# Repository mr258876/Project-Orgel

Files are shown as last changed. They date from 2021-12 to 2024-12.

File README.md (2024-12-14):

# Project Orgel
>### 赛博音乐盒计划第一部分
>### Cyber Musicbox Project Part I

- [中文](#中文)
- [English](#english)

# 中文
>## 目录
- [项目状态](#项目状态)
- [配件](#配件)
- [某个简短的改装指南](#某个简短的改装指南)
    - [传动改造](#传动改造)
    - [八音盒及电机的固定](#八音盒及电机的固定)
    - [电路搭建](#电路搭建)
- [控制程序烧录](#控制程序烧录)
- [使用指南](#使用指南)
    - [初次使用](#初次使用)
    - [基本操作](#基本操作)
    - [菜单与设置](#菜单与设置)
    - [无线控制](#无线控制)

>## 项目状态
* 基础原理验证 ✔
* 基础 UI ✔
* 更多可在UI中调节的值 ✔
* UI 多语言支持 ✔
* 项目自述 ✔
* 无线控制 ✔
* 多平台支持 ✔

>## 配件
* 八音盒 (废话) *1
* 支持串口通信的单片机 *1
>ℹ注：推荐使用ESP32或nRF51802
* TMC2209 步进电机驱动模块 *1
>⚠注意：模块需要支持以串口方式与MCU进行通信
* 42BYGH40/39 步进电机 (高40/39mm) *1  
>ℹ注：可以是任意两相四线步进电机, 但其应能够提供足够力矩(推荐300mN\*m以上)
* 42步进电机支架 (可选) *1
* 0.4模齿轮(60齿以上，但不宜过大) *1
>ℹ注：齿轮越大越好，降低电机转速是减小噪音的有效方法
<br/>⚠注意：齿轮需要能够与电机输出轴匹配
* 旋转编码器 *1
* SSD1306 0.96 寸 OLED 模块 *1
* 电源 (Plan A): USB-C PD 诱骗器 *1, 支持PD快充协议的充电器 *1, MP1584 DC-DC 降压模块 *1
* 电源 (Plan B): 3.3/5/12v 多路输出电源模块 *1, 12v/2A 电源适配器 *1
* 用于固定八音盒与电机的木盒、木块等 *1
* 用于固定的M3螺丝、M3螺母若干

## 某个简短的改装指南
接下来的步骤组成了一个简短的安装指南。步骤供参考，可根据实际情况进行调整。
### 传动改造
如图所示，改装电动只需使用八音盒传动部分中的部分齿轮。由于避开了传动部分中的易损齿轮，对该齿轮损坏的八音盒进行改装不失为一个绝佳选择。
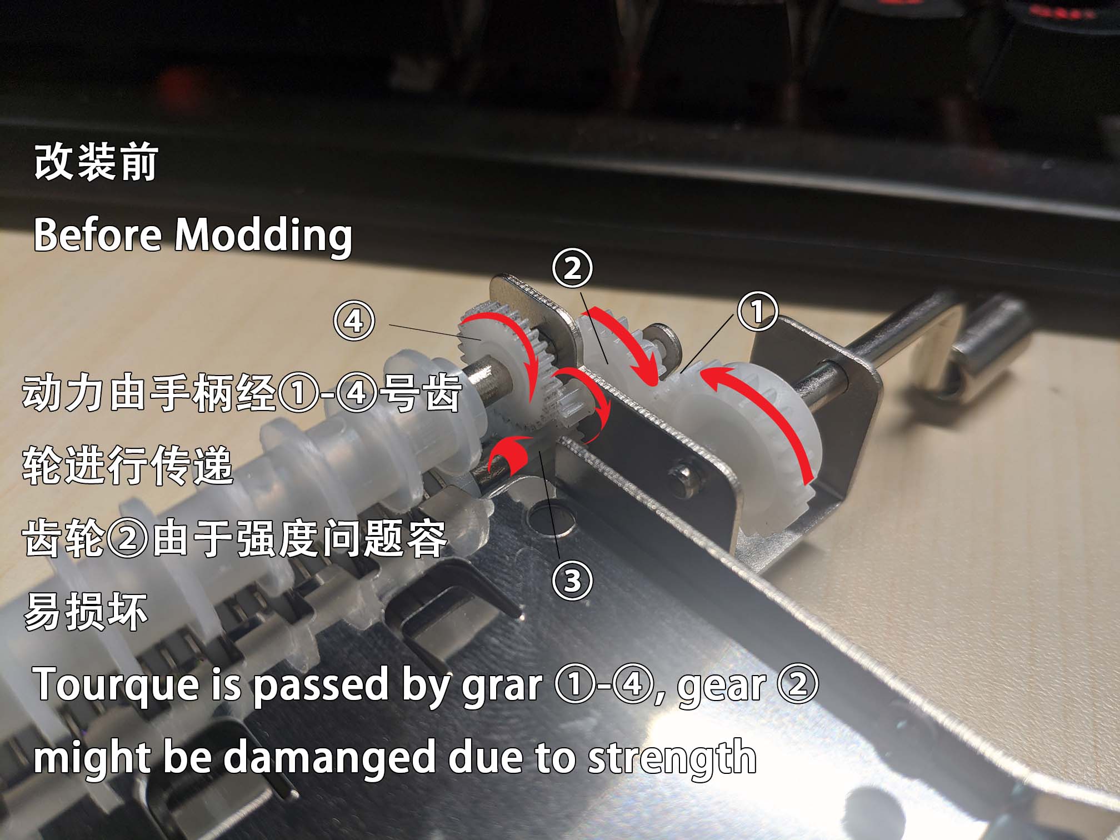
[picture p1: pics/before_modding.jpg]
before_modding

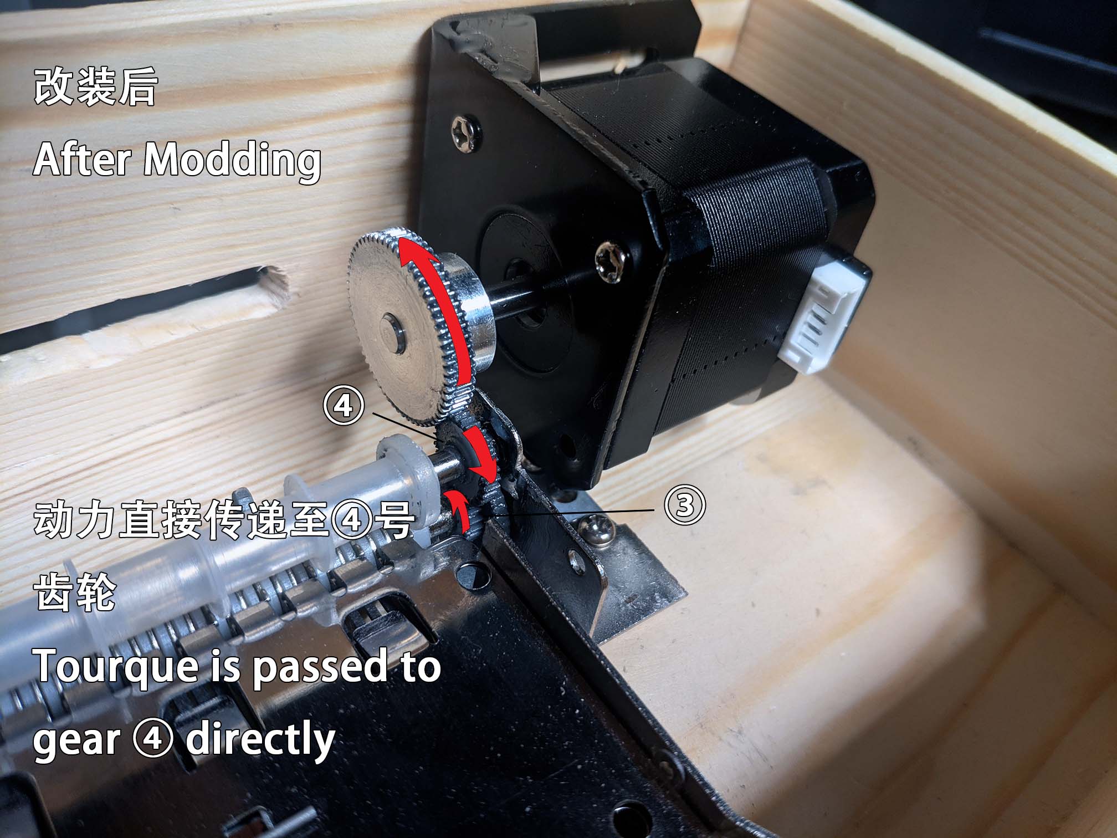
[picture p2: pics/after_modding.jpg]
after_modding


>⚠注意：在手摇八音盒中，手柄部分通常为噪音的源头之一。为了达到静音目的，断开手柄与其他齿轮间的传动是必要的。移除手柄或②号齿轮均可实现。图为移除了手柄及②号齿轮的八音盒。
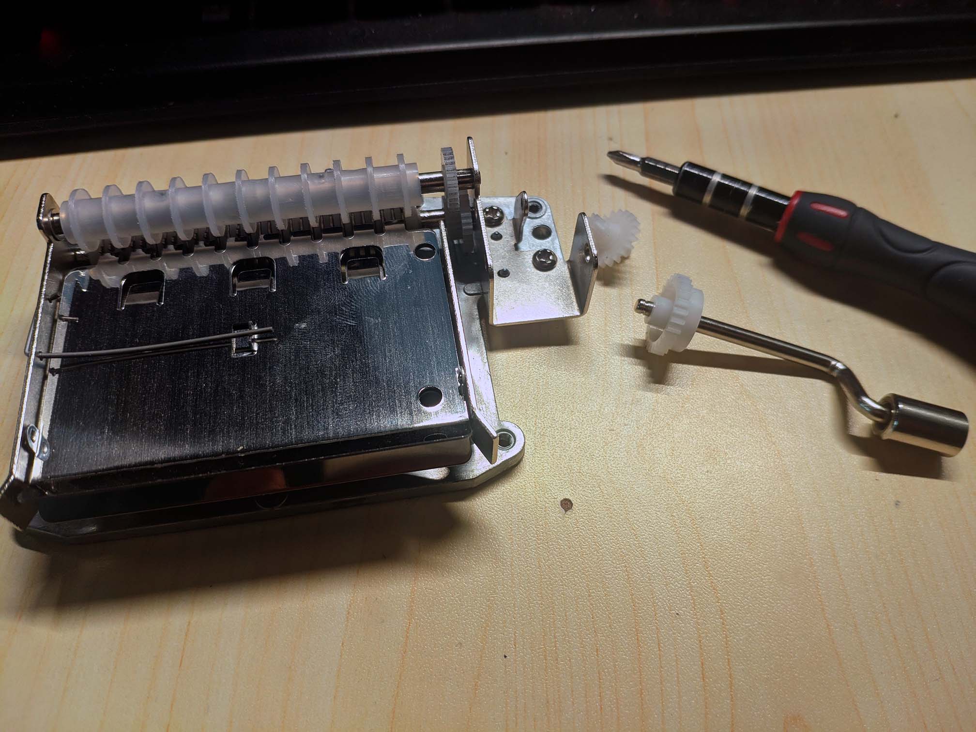
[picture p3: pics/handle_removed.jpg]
handle_removed

### 八音盒及电机的固定
毫无疑问，电机需要与八音盒固定在一起以进行传动。该部分有较多方案可供选择，故此处将不做较多阐述，实际应用时可不必遵照。

>⚠注意：不论以何种方式固定，**电机齿轮必须尽量与八音盒齿轮紧密配合**，否则可能会产生噪音并损坏齿轮。

考虑到八音盒可能需要一个共鸣腔，推荐将八音盒与电机固定在木盒中。如不考虑共鸣，或不方便对木盒进行钻孔/开槽，则也可固定在木块或其他材料上。此处以固定在木盒中为例。

由于42电机的体积较大，因此八音盒原配木盒大概率需要进行更换。目前市面上有多种尺寸木盒可供选择。上一节示例中的木盒尺寸为 长20cm\*宽13.5cm*高9cm。

#### 使用3D打印支架进行固定

项目提供了提供一个支架3D模型可进行参考。支架由两部分组成，分别负责替换原有支架与步进电机的固定。

[模型可在此下载](/Models/)

### 电路搭建

本项目提供两个不同平台版本：一个较为简易的使用ESP32开发板与其他现成部件进行搭建的版本，与一个从零开始构建的nRF51平台版本。您可以根据实际需要进行选择。

#### ESP32版本
`ESP32`版本基于现成部件，电路十分简单，如下图所示。

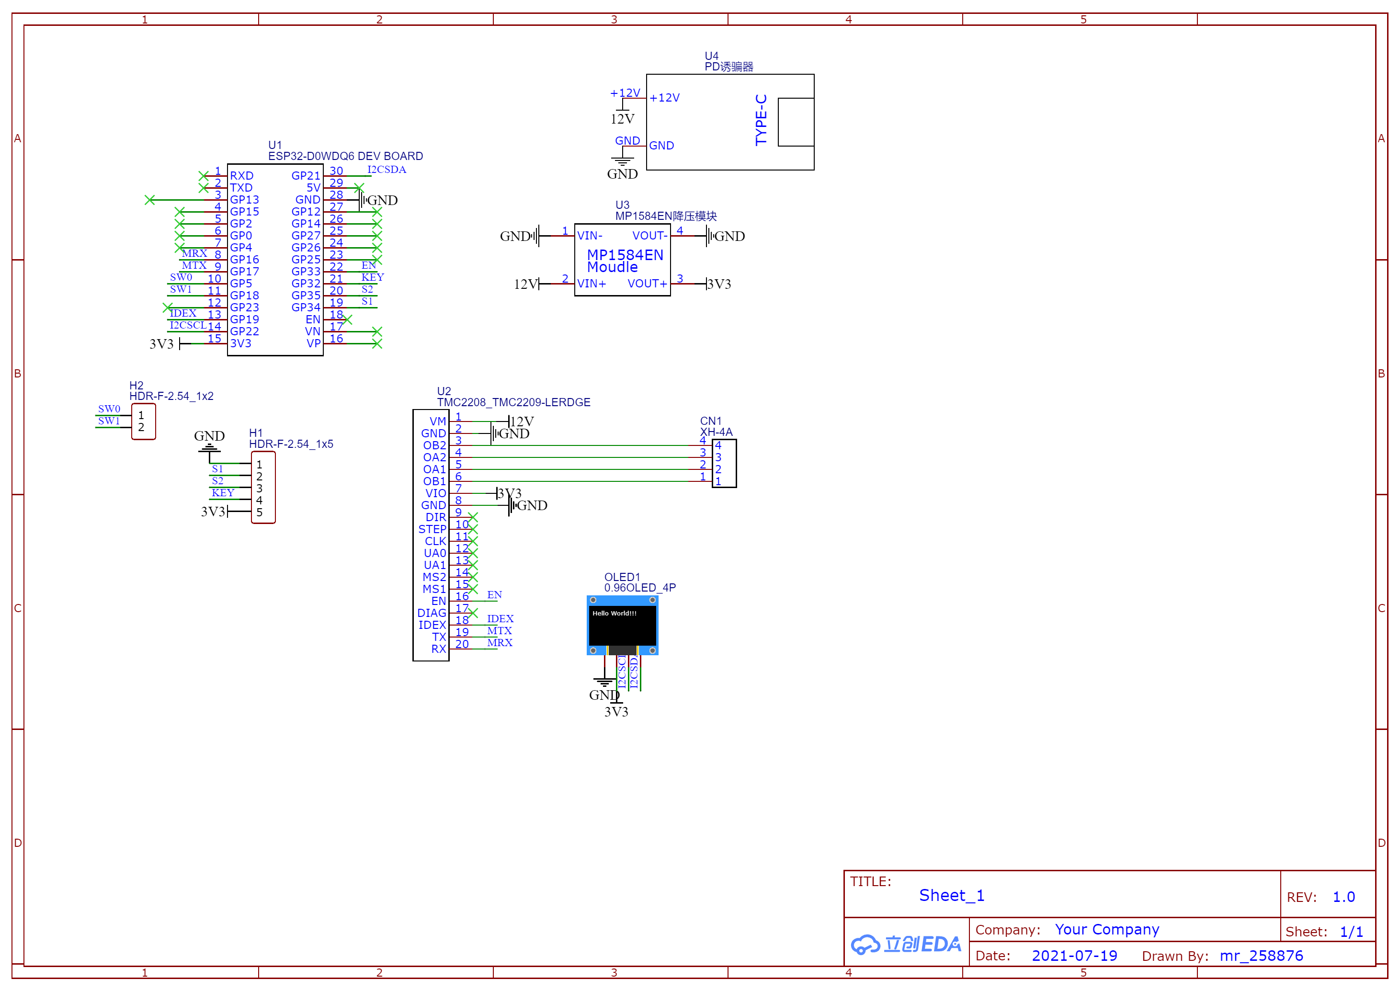
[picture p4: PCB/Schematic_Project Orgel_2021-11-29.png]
curcit_schema


处于空间利用方面的考量，推荐使用PCB实现上图中电路。[Gerber文件请点击这里][gerber_url]。
>ℹ注：仅适用于尺寸为22mm\*17mm的MP1584模块与焊接了TX,RX针脚的乐积TMC2209模块

如果无法进行焊接，该版本同样可以考虑使用面包板完成接线。

**ESP32版本参考BOM**
- 以下链接仅供参考，您可以根据实际情况自行购买
- 链接可能失效，如需更新请提起issue

| 商家 | 商品链接 | 款式 | 价格 (CNY) | 数量 | 备注 |
| ---- | ---- | ---- | ---- | ---- | ---- |
| 尚雅木艺 | [实木带锁复古收纳盒定制长方形大小号木盒子定做木质包装盒礼品盒](https://item.taobao.com/item.htm?id=610812897067) | 20\*13.5\*9 | 17.9 | 1 | 需自行开孔/开槽 (大概是整个项目最困难的部分) |
| 淮安善能机械有限公司 | [0.4模 60齿 孔5/6 顶丝 善能机械 铝齿轮 齿轮定制 小模数齿轮](https://item.taobao.com/item.htm?id=587174945136) | 60齿外径24.8/齿厚4/孔5台阶顶丝 | 9 | 1 | 不包邮 |
| 信泰微电子 | [ESP32-D0WDQ6开发板 蓝牙+WIFI模块 Lua物联网 米思齐图形化编程](https://item.taobao.com/item.htm?id=647797965965) | 30针 | 19.8 | 1 | 可能不太好找同款 |
| 信泰微电子 | [数字旋转编码器模块 转动电位器 旋转电位器 带旋钮帽](https://item.taobao.com/item.htm?id=576520367466) | - | 3.8 | 1 | - |
| 信泰微电子 | [0.96寸蓝色 黄蓝双色 白色 I2C IIC通信 显示器 OLED液晶屏模块](https://item.taobao.com/item.htm?id=43639171586) | 新款 颜色任意 | 10 | 1 | - |
| 信泰微电子 | [DC-DC 电源模块 降压稳压模块 车载电源 12V 5V转3.3V 固定输出](https://item.taobao.com/item.htm?id=534263863865) | - | 2.5 | 1 | - |
| 信泰微电子 | [XH2.54 2.54mm间距 白色座 接插件 直针座 4P XH2.54-4P连接线座](https://item.taobao.com/item.htm?id=36638833821) | - | 0.05 | 1 | 实际需要1个,但是不知道只买1个发不发货 |
| 微盛恒创电子 | [PD2.03.0诱骗器 触发转接笔记本电压可调9V12V15V 20VTYPE-C母头](https://item.taobao.com/item.htm?id=643246818193) | 12V | 4.8 | 1 | - |
| 乐积科技 | [3D打印机配件 TMC2209驱动大电流高细分替换2208A4988 LV8729模块](https://item.taobao.com/item.htm?id=610229295552) | - | 18.6 | 1 | 需要补齐四根空脚 |
| 布加特官方店 | [42/57步进电机支架安装固定座卧式支架电机马达支架座配带螺丝](https://item.taobao.com/item.htm?id=571691530940) | - | 1.7 | 1 | - |
| 布加特官方店 | [3D打印机配件42步进电机 驱动马达两相四线1.8度雕刻机42歩进马达](https://item.taobao.com/item.htm?id=559102944871) | 任意款式 XH-2.54配线 | 21.5 | 1 | - |
| telesky旗舰店 | [单排母双排母2.54mm排针母座排座针插座插针2.0 1/2/3/4/6/10-40P](https://item.taobao.com/item.htm?id=559102944871) | 1*2p单排母座2.54mm 20个 | 2.44 | 1 | 可选, 实际需要2个 |
| telesky旗舰店 | [单排母双排母2.54mm排针母座排座针插座插针2.0 1/2/3/4/6/10-40P](https://item.taobao.com/item.htm?id=559102944871) | 1*4p单排母座2.54mm 20个 | 2.75 | 1 | 可选, 实际需要1个 |
| telesky旗舰店 | [单排母双排母2.54mm排针母座排座针插座插针2.0 1/2/3/4/6/10-40P](https://item.taobao.com/item.htm?id=559102944871) | 1*5p单排母座2.54mm 20个 | 2.98 | 1 | 可选, 实际需要1个 |
| telesky旗舰店 | [单排母双排母2.54mm排针母座排座针插座插针2.0 1/2/3/4/6/10-40P](https://item.taobao.com/item.htm?id=559102944871) | 1*8p单排母座2.54mm 20个 | 3.59 | 1 | 可选, 实际需要2个 |
| telesky旗舰店 | [单排母双排母2.54mm排针母座排座针插座插针2.0 1/2/3/4/6/10-40P](https://item.taobao.com/item.htm?id=559102944871) | 1*15p单排母座2.54mm 10个 | 2.52 | 1 | 可选, 实际需要2个 |

#### nRF51版本
`nRF51`版本将主控、步进电机驱动、DCDC电路等部分集成在一块PCB上，进而减小了控制板体积，但同时也提升了制作难度。电路图如下所示。

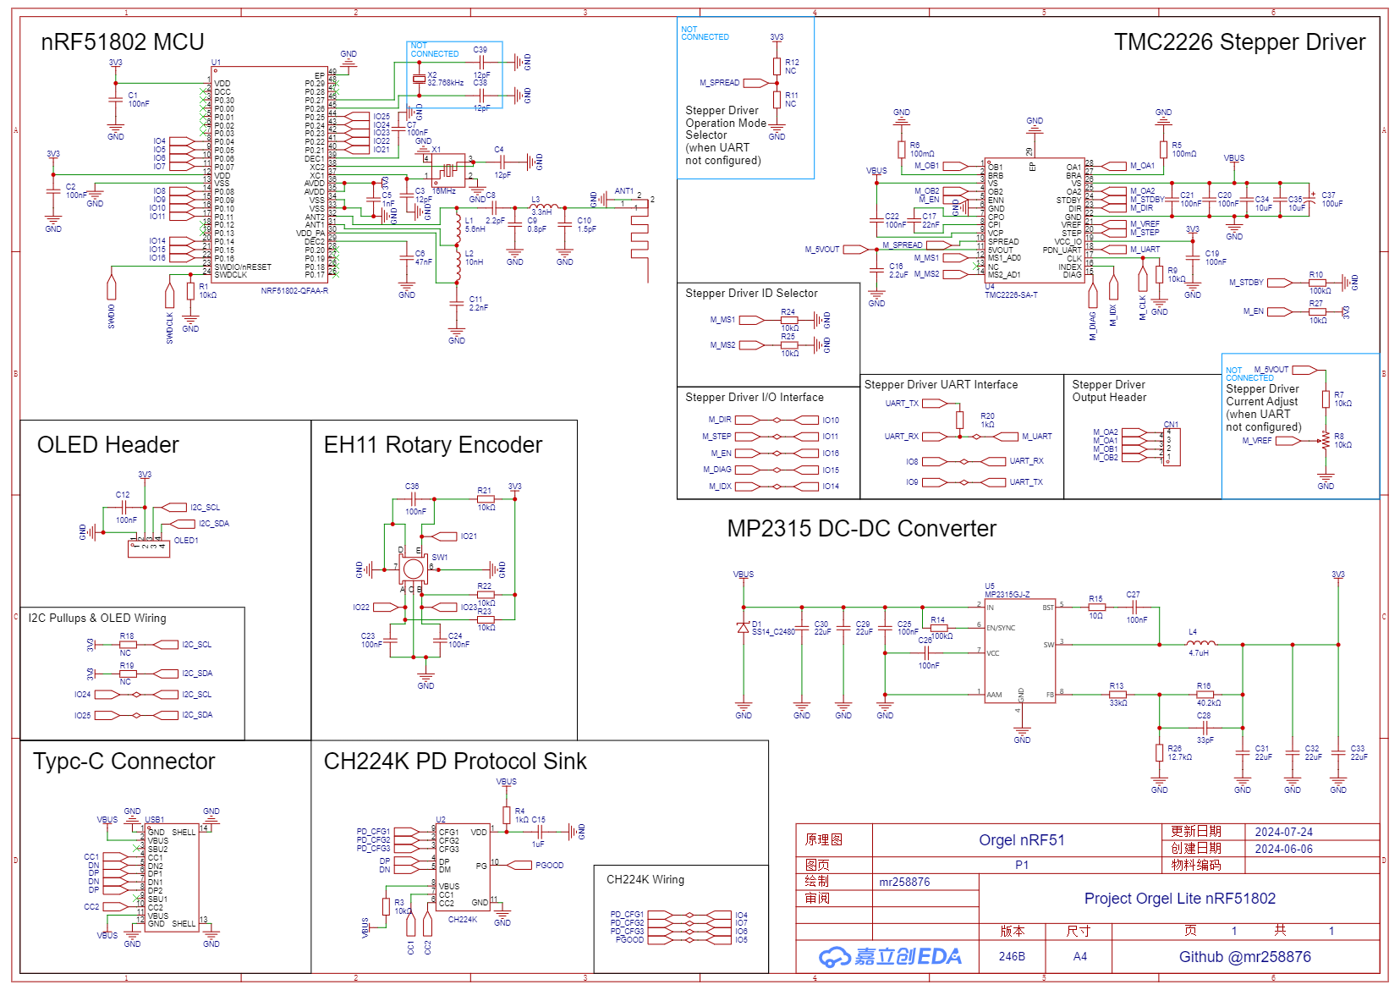
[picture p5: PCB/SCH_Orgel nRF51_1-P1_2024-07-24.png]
curcit_schema_nrf51


**项目BOM**

[项目BOM可在此处查看。][bom_url_nrf51]

**参考PCB**

[参考PCB可以在此处下载。][gerber_url_nrf51]

**焊接辅助工具**

[此处可查看对应焊接辅助工具。][solder_helper_url_nrf51]

## 控制程序烧录
改装的最后一步是将电机控制程序烧录至`ESP32`或`nRF51802/nRF51822`中。

您可以直接刷入 Release 中已编译好的固件，或自行使用Arduino编译并刷入。

### 刷入预编译固件

#### 为ESP32刷入预编译固件

0. 移步[乐鑫科技网站]("https://www.espressif.com.cn/zh-hans/support/download/other-tools")并下载`ESP Download Tool(Flash下载工具)`。</br>

1. 打开ESP Download Tool，芯片类型选择`ESP32`，工作模式选择`开发模式`。</br>
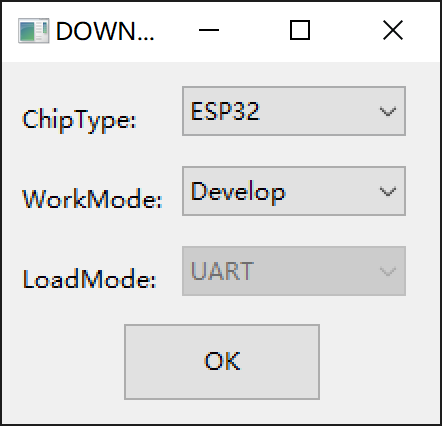
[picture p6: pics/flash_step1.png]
</br>
2. 按照下图设置刷入的文件、flash地址、flash速度，串口及下载速度按实际情况选择。</br>
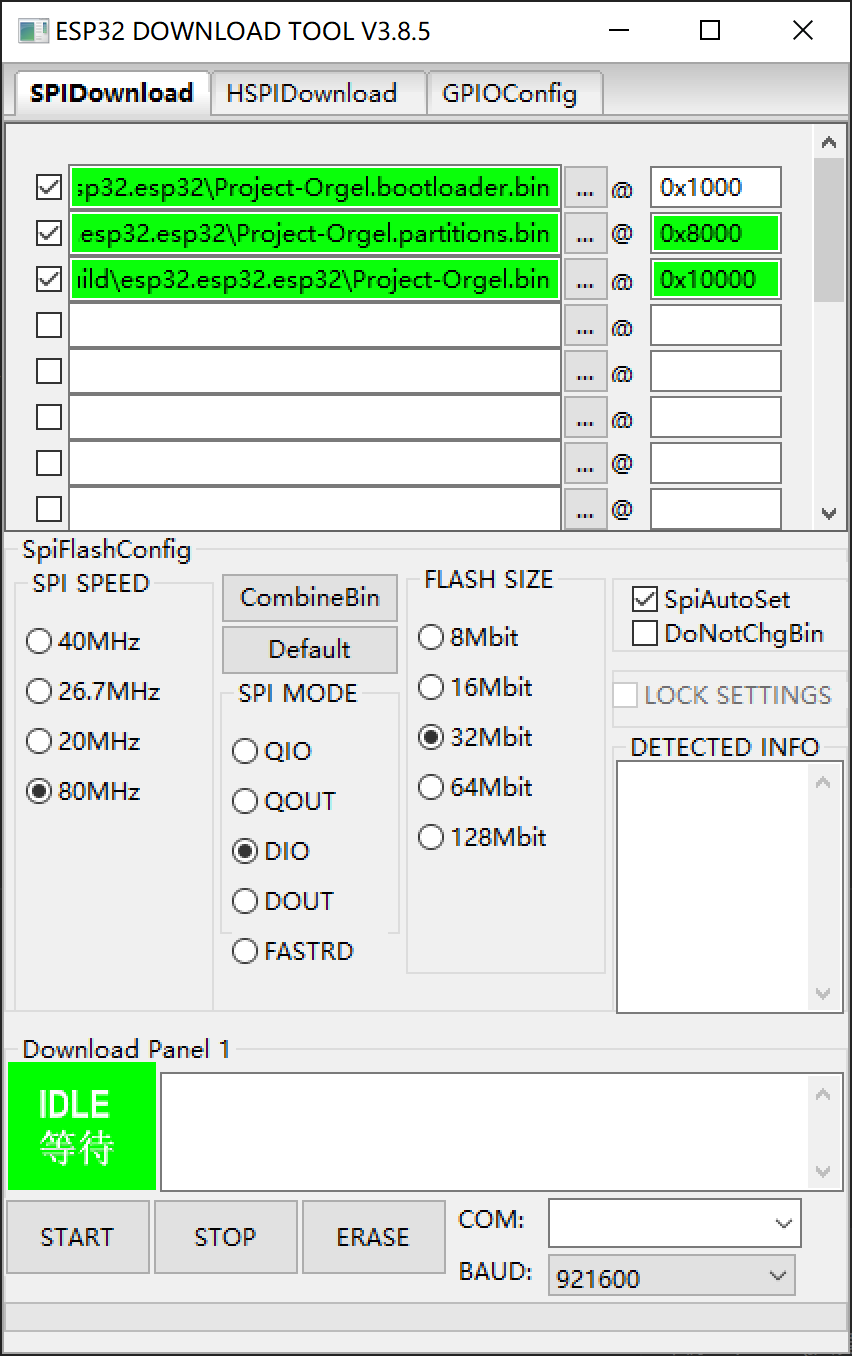
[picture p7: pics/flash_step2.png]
</br>
3. 点击`下载`按钮。当状态显示`完成`后，断开开发板与电脑的连接。</br>

#### 为nRF51刷入预编译固件

>ℹ注：为了向nRF51芯片刷入程序，您额外需要一个适用于ARM架构单片机的编程器，例如`ST-Link`、`J-Link`等。下方的流程以在Windows环境下使用`ST-Link`刷入为例，您可能需要根据实际情况适当修改命令行参数。

0. 移步[OpenOCD Github页面](https://github.com/openocd-org/openocd/releases)，下载并解压`OpenOCD`。</br>
1. 将编程器连接至控制板。
```
编程器             控制板
______         _____________
3V3   | ----> | 3V3   SWCLK | <-----,
GND   | ----> | GND   SWDIO | <--,  |
SWDIO | ----, |_____________|    |  |
SWCLK | --, `--------------------`  |
______|   `-------------------------`
```
2. 打开命令提示符(`CMD`)或`PowerShell`，并切换路径至`OpenOCD`文件夹中的`bin`目录下。</br>
3. 使用以下命令刷入预编译固件。在刷入完成后，命令行中应出现`** Verified OK **`提示。
   - 此处假设`Project-Orgel-nRF51.hex`与`openocd.exe`置于同一目录下。
   - 您可以根据实际情况将`st-link.cfg`替换为其他受支持的编程器配置文件。
```powershell
./openocd.exe -f "interface/st-link.cfg" -f "target/nrf51.cfg" -c "init" -c "reset halt" -c "nrf51 mass_erase" -c "program Project-Orgel-nRF51.hex verify reset exit"
```

### 自行编译并刷入

#### 为ESP32编译程序并刷入
首先需要在电脑上搭建Arduino-ESP32环境。[知乎用户铁熊的文章][zhihu_esp32_environment_url]可供参考。

在环境搭建完成后，还需要在库管理器中安装以下库：
```
tcMenu      @4.4.0
TMCStepper  @0.7.3
U8g2        @2.34.4
NimBLE      @1.4.2
```

准备完成后，使用Arduino IDE打开`Project-Oegel`文件夹中的`Project-Orgel.ino`进行烧录。

>⚠注意：Arduino IDE中的`esp32开发板`版本不可使用`3.0.0`及以上版本！

#### 为nRF51编译程序并刷入

对于`nRF51`版本，您需要将`arduino-esp32`开发环境替换为[n-able-Arduino](https://github.com/h2zero/n-able-Arduino)，具体操作如下：
1. 在`文件`->`首选项`->`附加开发板管理器网址`中添加链接`https://h2zero.github.io/n-able-Arduino/package_n-able_boards_index.json`
2. 待安装完成后，在`工具`->`开发板`->`Arm (Nim)BLE Boards`菜单中选择`Waveshare BLE400`开发板。
3. 在`工具`->`Low Frequency Clock`菜单中选择`Synthesized`选项。
4. 在`工具`->`编程器`菜单中选择`st-link v2`选项。

对于`nRF51`版本，您还需要将上述列表中的`U8g2`库替换为`SSD1306UTF8`库(基于`SSD1306Ascii`库)，请从[此处](https://github.com/mr258876/SSD1306UTF8)下载。

>ℹ注：对于`nRF51`版本，您需要点击`项目`菜单中的`使用编程器上传`选项刷入自编译程序。

## 使用指南
>⚠注意：由于硬件组合及改装操作的多样性，在不同情形下运行可能触发未知的bug，如部分功能不可用等。该指南仅代表在测试硬件上的操作及运行效果。

>🛑警告：步进电机驱动器运行会产生高温。请小心烫伤。

### 初次使用
将程序首次烧录至ESP32时，所有设置为默认初始值0。请遵照下述方法设置`齿轮齿数`、`运行电流`并保存后再使用。
### 基本操作
在主视图中，旋转旋钮更改BPM。单击旋钮切换播放状态。
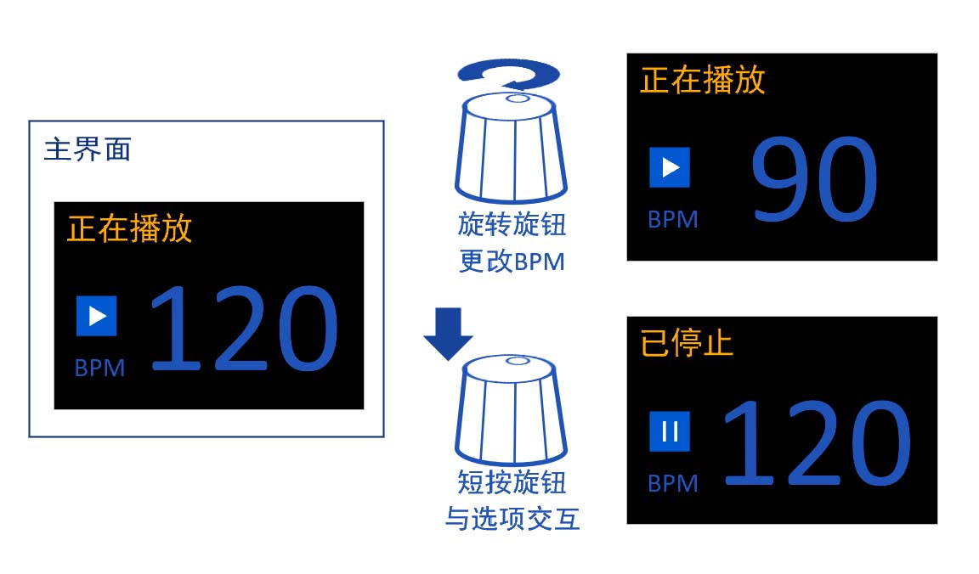
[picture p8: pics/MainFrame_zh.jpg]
mainframe_zh

### 菜单与设置
在主视图中长按可进入主菜单。
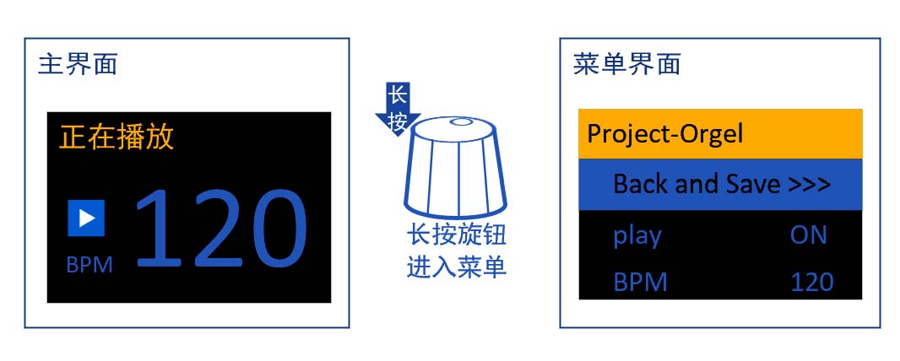
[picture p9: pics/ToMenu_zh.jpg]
tomenu_zh


在主菜单中选择`Back and Save`以保存设置并回到主菜单。在主菜单中无操作30秒会自动返回主界面。

>⚠注意：在更改菜单中选项值后必须通过`Back and Save`选项退出菜单，否则在重启后选项值将恢复更改前状态。

在菜单中旋转旋钮查看选项，单击旋钮以与选项交互。在交互状态下旋转旋钮以更改选项值，单击旋钮退出。
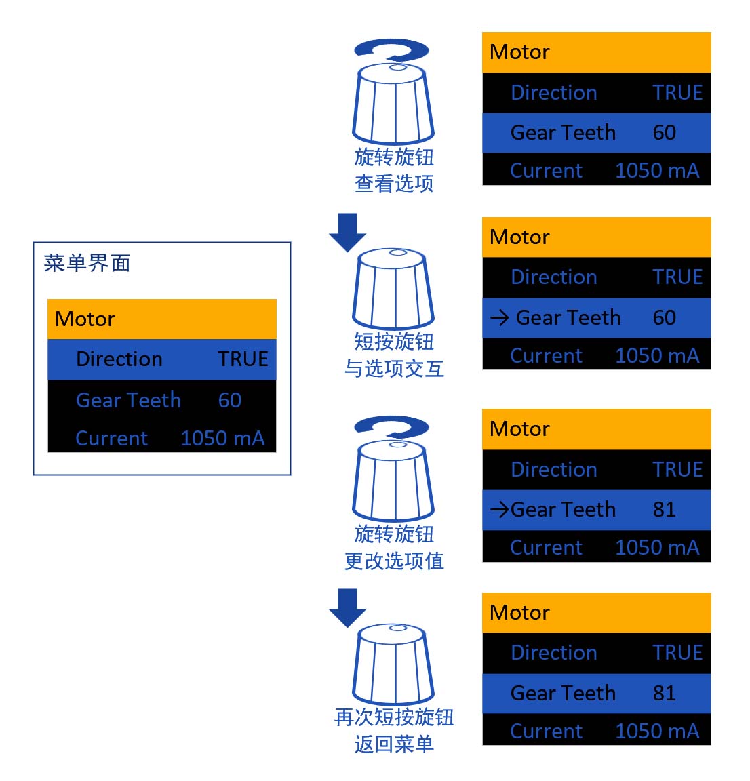
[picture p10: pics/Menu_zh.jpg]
menu_zh


各可调节值说明：
 - 电机设置
     - 反向运转: 控制电机正反转
     - 齿轮齿数: 电机齿轮齿数设置
     - 运行电流: 电机运行电流设置，单位mA 参考值：1050mA
    >⚠注意：随着电流的增大，驱动器会产生更多热量并可能导致过热保护，电机可能会产生更大噪音。正常使用请不要将该值提升至1700mA以上。
 - 语言
     - ENG：英语
     - 中文：简体中文
 - 蓝牙
     - 开：开启蓝牙并启用无线控制功能
     - 关：关闭蓝牙并停用无线控制功能

### 无线控制

> 请打开设置中的蓝牙开关，随后访问[https://mr258876.github.io/Project-Orgel/](https://mr258876.github.io/Project-Orgel/)并按提示操作。

Have fun!

# English
>## Table of Contents
- [Project Orgel](#project-orgel)
- [中文](#中文)
  - [某个简短的改装指南](#某个简短的改装指南)
    - [传动改造](#传动改造)
    - [八音盒及电机的固定](#八音盒及电机的固定)
      - [使用3D打印支架进行固定](#使用3d打印支架进行固定)
    - [电路搭建](#电路搭建)
      - [ESP32版本](#esp32版本)
      - [nRF51版本](#nrf51版本)
  - [控制程序烧录](#控制程序烧录)
    - [刷入预编译固件](#刷入预编译固件)
      - [为ESP32刷入预编译固件](#为esp32刷入预编译固件)
      - [为nRF51刷入预编译固件](#为nrf51刷入预编译固件)
    - [自行编译并刷入](#自行编译并刷入)
      - [为ESP32编译程序并刷入](#为esp32编译程序并刷入)
      - [为nRF51编译程序并刷入](#为nrf51编译程序并刷入)
  - [使用指南](#使用指南)
    - [初次使用](#初次使用)
    - [基本操作](#基本操作)
    - [菜单与设置](#菜单与设置)
    - [无线控制](#无线控制)
- [English](#english)
  - [Hardware Requirements](#hardware-requirements)
  - [A Brief Modding Guide](#a-brief-modding-guide)
    - [Gear Modding](#gear-modding)
    - [Mounting](#mounting)
    - [Circuit](#circuit)
    - [Uploading Code](#uploading-code)
      - [Flash the compiled firmware](#flash-the-compiled-firmware)
      - [Compile and flash by yourself](#compile-and-flash-by-yourself)
  - [Usage](#usage)
    - [First Use](#first-use)
    - [Basic Operations](#basic-operations)
    - [Settings](#settings)
    - [Wireless Control](#wireless-control)

>## Project Status 
* Make it work  ✔
* A Basic UI    ✔
* More Adjustable Values in UI ✔
* UI MultiLanguage Support   ✔
* Readme  ✔
* Wireless Control ✔
* Multi Platform Support ✔

## Hardware Requirements
* Musicbox (of course) *1
* ESP32-D0DWQ6 Dev Moudle 30pin *1
* TMC2209 Stepper Driver Module *1
>⚠Caution: the driver moudlue should be able to communicate with the MCU through UART or Serial port.
* 42BYGH40/39 NEMA17 Stepper *1  
>ℹNote: Could be replaced with any 2-phase 4-wire step motor, however it should provide enough torque(recommand 300mN*m or above).
* NEMA17 Motor Stand (optional) *1
* 0.4M gear(At least 60 teeth, but not too big) *1  
>ℹNote：It is a good idea to have a bigger gear, reducing the motor speed is an effective way to reduce noise.
<br/>⚠Caution: The gear should be able to match the output shaft of the motor.
* Rotatry Encoder *1
* SSD1306 0.96 inch OLED Screen *1
* Power Supply (Plan A): USB-C PD Trigger/Decoy *1, Phone charger with fast charging support *1, MP1584 DC-DC step-down moudle *1
* Power Supply (Plan B): 3.3/5/12v multi-output power moudle *1, 12v/2A AC/DC adapter *1
* Box or something else for mounting musicbox and motor *1
* M3 Screws & Nuts for Mounting

## A Brief Modding Guide
The following steps constitute a biref modding guide, which you could refer to but don’t have to strictly follow.
### Gear Modding
Only some of all gears in the musicbox will be used after the modding, as shown in the picture below. Avoiding the vulnerable gear(gear #2), it is a good choice to mod a musicbox with that gear damaged.
before_modding
after_modding

>⚠Caution：The handle is usually one of the main noise source. In order to get silent, it is necessary to disconnect the transmission between the handle and other gears, which could be implemented by removing the handle or gear #2. A music box with handle and gear #2 removed is as shown. handle_removed
### Mounting
Without doubt, the motor needs to be mounted with the musicbox. With many solutions avilable, there will not be much description here, and you don't have to follow.

>⚠Caution: No matter how they are mounted, **the gear of motor have to work as close as possible**, or there will might be noise and the gear may got damange.

Considering that the music box may need a resonance cavity, it is recommended to fix the music box and the motor in a wooden box. If resonance is not considered, or it is inconvenient to drill/slot the wooden box, it can also be fixed on a wooden block or other materials. Take fixing in a wooden box as an example

Due to the ize of the NEMA-17 motor, the original wooden box of the music box will most likely need to be replaced. There are many sizes of wooden boxes available on the market. The size of the wooden box in the example in the previous section is L20cm * W13.5cm * H9cm.
### Circuit
The circuit used in this project is simple, schematic as shown below.

curcit_schema

Considerated in space utilization, using a PCB to imply the curcit is recommedned. As a beginner of drawing PCB, only a poor board could be provided. Click [here][gerber_url] if you would take a look.
>ℹNote：Only applies to MP1584 with size 2mm\*17mm and Lerdge TMC2209 module with TX/RX pin soldered.

Using a breadboard to apply the cutcit also works.

### Uploading Code
The last step is to upload the controlling program to the ESP32.

You can flash the compiled firmware directly into Release, or use Arduino to compile and flash it yourself.

#### Flash the compiled firmware

0. Go to [Espressif Technology website]("https://www.espressif.com.cn/en/support/download/other-tools") and download `ESP Download Tool`. </br>

1. Open ESP Download Tool, select `ESP32` for chip type, and `Development Mode` for working mode. </br>
</br>
2. Set the flashed file, flash address, flash speed, serial port and download speed according to the actual situation according to the figure below. </br>
</br>
3. Click the `Download` button. When the status shows `Done`, disconnect the development version from the computer. </br>

#### Compile and flash by yourself

First, you will need an Arduino-ESP32 environment. There's a [guide from randomnerdtutorials][randomnerdtutorials_esp32_environment_url] could be used as a reference.

For `ESP32` devices, he following libraries are also required after building up the environment:
```
tcMenu      @4.2.1
TMCStepper  @0.7.3
U8g2        @2.34.4
NimBLE      @1.4.2
```

For `nRF51` devices, you need to replace `U8g2` in the list above as an MODDED `SSD1306Ascii` library, which could be found [here](https://github.com/mr258876/SSD1306Ascii).

After that, open `Project-Orgel.ino` in folder `Project-Oegel` with Arduino-IDE to upload.

>⚠Note：`esp32` version in Arduino IDE should be below `3.0.0`, or compilation will fail!

## Usage
>⚠Caution: Due to the diversity of hardware bundles and differences in modding procedure, unknown bugs might appear in some situations (e.g. functions not working). This manual only represents the operations and results on the testing hardware.

>🛑Warning: The driver moudle would generate heat. Please be aware of burns.

### First Use
When first upload the code to ESP32, all setting values will be default to 0. Please set `Geat Teeth`, `Current` by following the methods below before use.
### Basic Operations
In the main view, change BPM by rotating the knob, switch playback status by pressing the knob once.
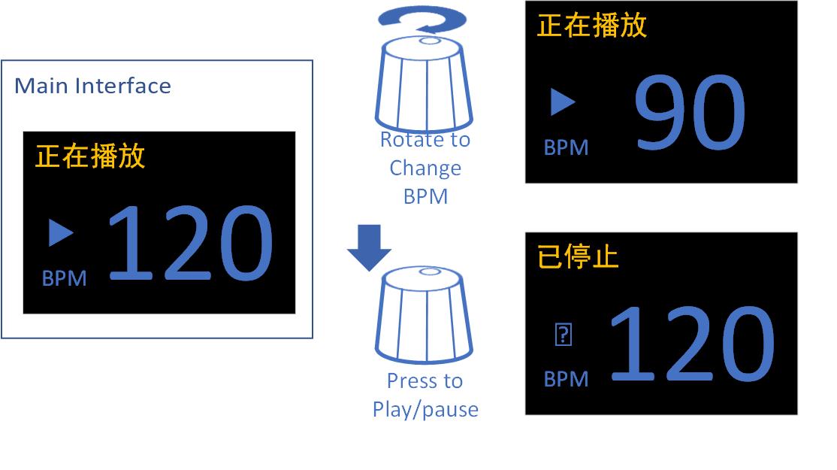
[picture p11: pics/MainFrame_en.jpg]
mainframe_en

### Settings
Pressing down the knob and hold for few seconds to go to the menu.
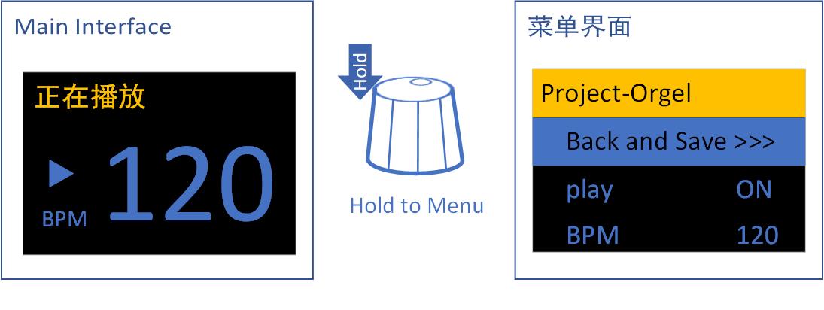
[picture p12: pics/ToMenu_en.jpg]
tomenu_en


Select `Back and Save` in menu to save the settings and back to main view. After entered the menu, it will go back to the main view without saving automatically with no action in 30 secs。

>⚠Caution: Exiting through `Back and Save` option is required after changing any value in the settings menu, or the values will restore after reboot.

In the menu, rotate the knob to go through, intract with options by pressing down once. Change the option value by rotating the knob when option is acticed, and pressing down once to go back to menu.
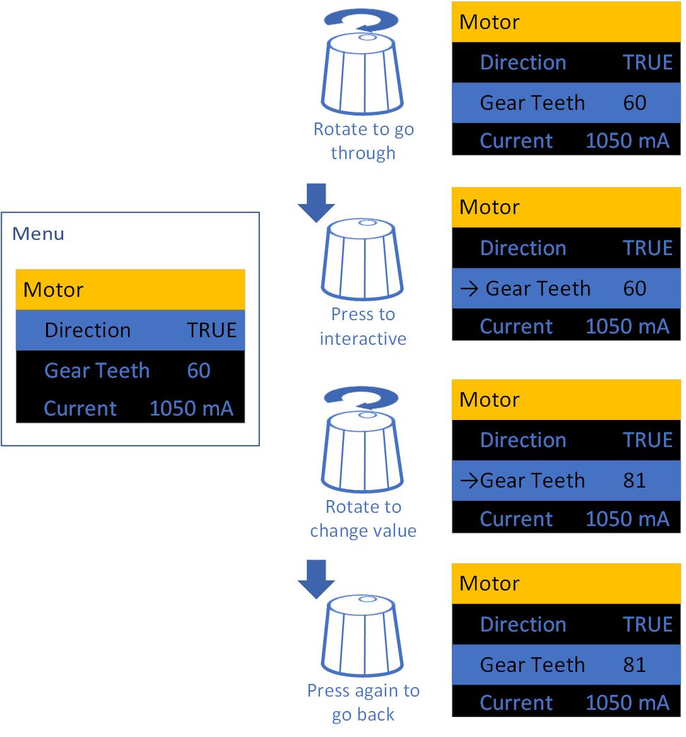
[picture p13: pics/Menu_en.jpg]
menu_en


Explations on adjustable values:
 - Motor
     - Reversed: To reverse the motor operation direction.
     - Gear Teeth: Teeth number of the gear installed on the motor. Related to running speed.
     - Current: The runing current of motor in mA. Reference value: 1050mA. 
    >⚠Caution：The Driver moudle would produce more heat as the current goes up, and might trigger overheat protection. The motor will produce more noise as well. Do not raise this value over 1700mA in normal use.
 - Language
     - ENG: English
     - 中文: Simplified Chinese
 - Bluetooth
     - On: Turn on bluetooth, and enable wireless control
     - Off: Turn off bluetooth, and disable wireless control

### Wireless Control

> Turn ON the `bluetooth` option in settings menu, then visit [https://mr258876.github.io/Project-Orgel/](https://mr258876.github.io/Project-Orgel/).

Have fun!

[before_modding_url]:/pics/before_modding.jpg
[after_modding_url]:/pics/after_modding.jpg
[handle_removed_url]:/pics/handle_removed.jpg

[schema_url]:/PCB/Schematic_Project%20Orgel_2021-11-29.png
[gerber_url]:/PCB/Gerber_PCB_Project%20Orgel.zip

[bom_url_nrf51]:/PCB/BOM_Board1_Orgel%20nRF51_2024-07-24.xlsx
[schema_url_nrf51]:/PCB/SCH_Orgel%20nRF51_1-P1_2024-07-24.png
[gerber_url_nrf51]:/PCB/Gerber_PCB1_Orgel%20nRF51_2024-07-24.zip
[solder_helper_url_nrf51]:https://raw.githubusercontent.com/mr258876/Project-Orgel/raw/main/PCB/Solder_Helper_PCB1_Orgel%20nRF51_2024-7-24.html

[zhihu_esp32_environment_url]:https://zhuanlan.zhihu.com/p/107804270
[randomnerdtutorials_esp32_environment_url]:https://randomnerdtutorials.com/installing-the-esp32-board-in-arduino-ide-windows-instructions/

[mainframe_zh_url]:/pics/MainFrame_zh.jpg
[tomenu_zh_url]:/pics/ToMenu_zh.jpg
[menu_zh_url]:/pics/Menu_zh.jpg

[mainframe_en_url]:/pics/MainFrame_en.jpg
[tomenu_en_url]:/pics/ToMenu_en.jpg
[menu_en_url]:/pics/Menu_en.jpg

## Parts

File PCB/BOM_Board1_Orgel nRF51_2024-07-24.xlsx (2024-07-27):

No. | Quantity | Comment | Designator | Footprint | Value | Manufacturer Part | Manufacturer | Supplier Part | Supplier | Pins
1 | 14 | 100nF | C1,C2,C7,C12,C19,C20,C21,C22,C23,C24,C25,C26,C27,C36 | C0603 | 100nF | CC0603KRX7R9BB104 | YAGEO(国巨) | C14663 | LCSC | 2
2 | 2 | 12pF | C3,C4 | C0603 | 12pF | CL10C120JB8NNNC | SAMSUNG(三星) | C38523 | LCSC | 2
3 | 1 | 1nF | C5 | C0603 | 1nF | CL10B102KB8NNNC | SAMSUNG(三星) | C1588 | LCSC | 2
4 | 1 | 47nF | C6 | C0603 | 47nF | CL10B473KB8NNNC | SAMSUNG(三星) | C1622 | LCSC | 2
5 | 1 | 2.2pF | C8 | C0603 | 2.2pF | 0603CG2R2C500NT | FH(风华) | C1651 | LCSC | 2
6 | 1 | 0.8pF | C9 | C0603 | 0.8pF | 0603CG0R8B500NT | FH(风华) | C507057 | LCSC | 2
7 | 1 | 1.5pF | C10 | C0603 | 1.5pF | 0603CG1R5C500NT | FH(风华) | C1639 | LCSC | 2
8 | 1 | 2.2nF | C11 | C0603 | 2.2nF | GRM1885C1H222JA01D | muRata(村田) | C77033 | LCSC | 2
9 | 1 | 1uF | C15 | C0603 | 1uF | CL10A105KB8NNNC | SAMSUNG(三星) | C15849 | LCSC | 2
10 | 1 | 2.2uF | C16 | C0603 | 2.2uF | CL10A225KB8NNNC | SAMSUNG(三星) | C913904 | LCSC | 2
11 | 1 | 22nF | C17 | C0603 | 22nF | CL10B223KB8NNNC | SAMSUNG(三星) | C21122 | LCSC | 2
12 | 1 | 33pF | C28 | C0603 | 33pF | CL10C330JB8NNNC | SAMSUNG(三星) | C1663 | LCSC | 2
13 | 5 | 22uF | C29,C30,C31,C32,C33 | C0805 | 22uF | CGA0805X5R226M350MT | HRE(芯声) | C6119901 | LCSC | 2
14 | 2 | 10uF | C34,C35 | C1206 | 10uF | CL31A106KBHNNNE | SAMSUNG(三星) | C13585 | LCSC | 2
15 | 1 | 100uF | C37 | CAP-SMD_BD6.3-L6.6-W6.6-LS7.6-RD | 100uF | RVT1H101M0607 | ROQANG(容强) | C3151829 | LCSC | 2
16 | 1 | XH-4AW | CN1 | CONN-TH_XH-4AW |  | XH-4AW | HCTL(华灿天禄) | C2908613 | LCSC | 4
17 | 1 | SS14 | D1 | SMA_L4.2-W2.6-LS5.3-RD |  | SS14 | MDD | C2480 | LCSC | 2
18 | 1 | 5.6nH | L1 | IND-SMD_L1.6-W0.8-1 | 5.6nH | LQW18AN5N6C00D | muRata(村田) | C98081 | LCSC | 2
19 | 1 | 10nH | L2 | IND-SMD_L1.6-W0.8-1 | 10nH | LQW18AN10NG00D | muRata(村田) | C86131 | LCSC | 2
20 | 1 | 3.3nH | L3 | L0603 | 3.3nH | SDCL1608C3N3STDF | Sunlord(顺络) | C27274 | LCSC | 2
21 | 1 | 4.7uH | L4 | IND-SMD_L5.4-W5.2_FXL0530 | 4.7uH | FXL0530-4R7-M | cjiang(长江微电) | C177246 | LCSC | 2
22 | 1 | 2.54-1*4P母 | OLED1 | HDR-TH_4P-P2.54-V-F |  | 2.54-1*4P母 | BOOMELE(博穆精密) | C2718488 | LCSC | 4
23 | 9 | 10kΩ | R1,R3,R7,R9,R21,R22,R23,R24,R25 | R0603 | 10kΩ | 0603WAF1002T5E | UNI-ROYAL(厚声) | C25804 | LCSC | 2
24 | 2 | 1kΩ | R4,R20 | R0603 | 1kΩ | 0603WAF1001T5E | UNI-ROYAL(厚声) | C21190 | LCSC | 2
25 | 2 | 100mΩ | R5,R6 | R1206 | 100mΩ | 1206W4F100LT5E | UNI-ROYAL(厚声) | C25334 | LCSC | 2
26 | 1 | 10kΩ | R8 | RES-ADJ-SMD_3P-L3.0-W3.8-P1.75-BR | 10kΩ | TC33X-2-103E | BOURNS | C719176 | LCSC | 3
27 | 2 | 100kΩ | R10,R14 | R0603 | 100kΩ | 0603WAF1003T5E | UNI-ROYAL(厚声) | C25803 | LCSC | 2
28 | 1 | 33kΩ | R13 | R0603 | 33kΩ | 0603WAF3302T5E | UNI-ROYAL(厚声) | C4216 | LCSC | 2
29 | 1 | 10Ω | R15 | R0603 | 10Ω | 0603WAF100JT5E | UNI-ROYAL(厚声) | C22859 | LCSC | 2
30 | 1 | 40.2kΩ | R16 | R0603 | 40.2kΩ | 0603WAF4022T5E | UNI-ROYAL(厚声) | C12447 | LCSC | 2
31 | 1 | 12.7kΩ | R26 | R0603 | 12.7kΩ | 0603WAF1272T5E | UNI-ROYAL(厚声) | C22866 | LCSC | 2
32 | 1 | EC11E15244B2 | SW1 | SW-TH_EC11XXXXXXXX |  | EC11E15244B2 | ALPSALPINE(阿尔卑斯阿尔派) | C470754 | LCSC | 7
33 | 1 | NRF51802-QFAA-R | U1 | UQFN-48_L6.0-W6.0-P0.40-BL-EP4.6 |  | NRF51802-QFAA-R | NORDIC | C167636 | LCSC | 49
34 | 1 | CH224K | U2 | ESSOP-10_L4.9-W3.9-P1.0-LS6.0-TL-EP |  | CH224K | WCH(南京沁恒) | C970725 | LCSC | 11
35 | 1 | TMC2226-SA-T | U4 | HTSSOP-28_L9.8-W4.5-P0.65-LS6.6-BL-EP |  | TMC2226-SA-T | TRINAMIC | C705366 | LCSC | 29
36 | 1 | MP2315GJ-Z | U5 | TSOT-23-8_L2.9-W1.6-P0.65-LS2.8-BR |  | MP2315GJ-Z | MPS(芯源) | C45889 | LCSC | 8
37 | 1 | TYPE-C 16PIN 2MD(073) | USB1 | USB-C-SMD_TYPE-C-6PIN-2MD-073 |  | TYPE-C 16PIN 2MD(073) | SHOU HAN(首韩) | C2765186 | LCSC | 14
38 | 1 | 16MHz | X1 | CRYSTAL-SMD_4P-L2.0-W1.6-BL | 16MHz | XL7EL89CLI-111YLC-16M | YXC(扬兴晶振) | C2965578 | LCSC | 4

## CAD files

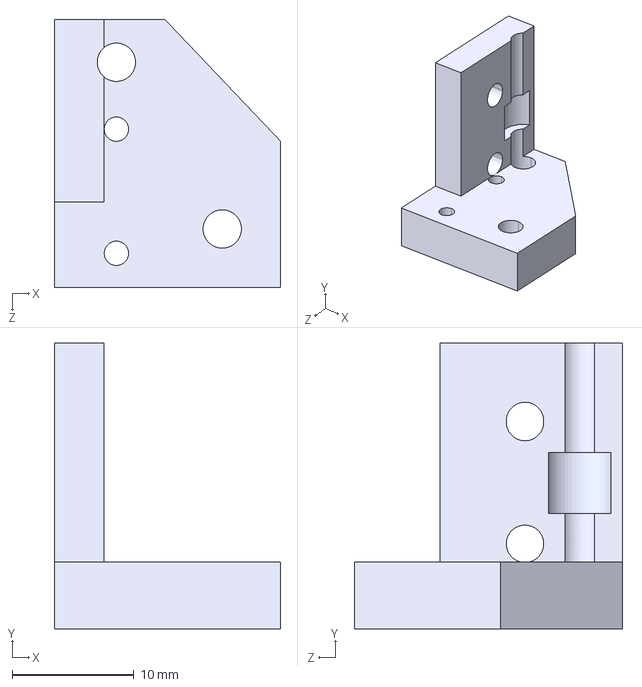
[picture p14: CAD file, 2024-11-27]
Models/Support 1.STEP
18.6 x 23.5 x 22.0 mm

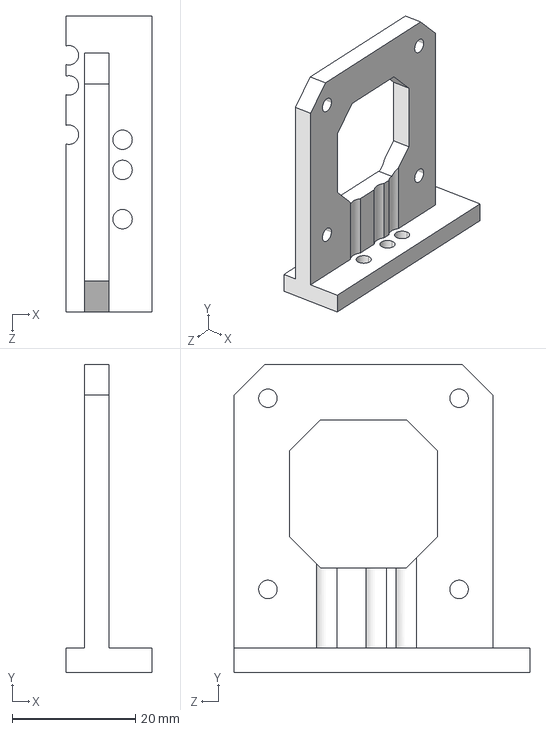
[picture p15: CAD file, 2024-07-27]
Models/Support 2.STEP
14.0 x 50.0 x 48.0 mm

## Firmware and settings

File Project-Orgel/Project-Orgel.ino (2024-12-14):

#include "pinouts.h"

#include "Project-Orgel_menu.h"
// default CPP main file for sketch
#include <PlatformDetermination.h>
#include <TaskManagerIO.h>

#include "ThemeProjOrgel.h"
#include "HomepageProjOrgel.h"

#include <HardwareSerial.h>
#include <TMCStepper.h>

#include "lv_i18n.h"

#include <NimBLEDevice.h> // Bluetooth
#include "BLEInterface.h"

#include "PowerManager.h"

#ifndef NRF51
#include "u8g2_wqy_14_project_orgel.h"
#endif

#if SOC_UART_NUM > 2
#define DRIVER_SERIAL Serial2 // TMC2209 Serial Port
#elif SOC_UART_NUM > 1
#define DRIVER_SERIAL Serial1 // ESP32C3 have only 2 serial ports
#else
#define DRIVER_SERIAL Serial // nRF51 have only 1 serial port
#endif

#define DRIVER_ADDRESS 0b00 // Serial Address

#ifndef NRF51
#define R_SENSE 0.11f // Match to your driver <- Refer "Selecting Sense Resistors" section in datasheet
#else
#define R_SENSE 0.12f // Refer to schema
#endif

// 电机内部输出轴旋转一周步数
#define STEPS_PER_ROTOR_REV 200 // 42电机 一圈200
#define DRIVER_MICROSTEPS 8
// 输出轴减速比
#define GEAR_REDUCTION 1.0f // 42电机 输出轴直出
// 八音盒减速比
#define ORGEL_GEAR 29 // 29齿八音盒齿轮
// 八音盒齿轮周拍
#define ORGEL_BPM_PER_ROUND 4.51603944f // 齿轮周长约1.15picm,纸带一拍0.8cm,故八音盒齿轮旋转一周约4.516拍
// 获得BPM计算常数
// const double BPM_CALC_CONST = STEPS_PER_ROTOR_REV * GEAR_REDUCTION * ORGEL_GEAR / MOTOR_GEAR / ORGEL_BPM_PER_ROUND / 60;
const float BPM_CALC_CONST = STEPS_PER_ROTOR_REV * DRIVER_MICROSTEPS * GEAR_REDUCTION * ORGEL_GEAR / ORGEL_BPM_PER_ROUND / 60; // <- 电机齿轮现在由菜单赋值并在设置BPM时计算齿轮比

// Create a Driver Object
TMC2209Stepper driver(&DRIVER_SERIAL, R_SENSE, DRIVER_ADDRESS);

// Power Manager
PowerManager pm(CH224K_PG_Pin, CH224K_CFG1_Pin, CH224K_CFG2_Pin, CH224K_CFG3_Pin);

// Variables
bool playStatus = false;
int16_t playBPM = 120;
float bpmTweak = 1.0;
int16_t motorCurrent = 500;
bool autoCurrentEnabled;
bool motorDirection;
int16_t motorGear = 60;
bool lastPowerStatus = false;

////////// FUNCTION PROTOTYPES //////////
static void syncValuesFromBluetooth();
static void storeNvsDefaults();
static void installTheme();
static void powerSetup();
static void checkPowerStatus();
static void driverSetup();
static void updateMotorParams();

////////// FUNCTIONS ///////////
void setup()
{
#if defined(ESP_PLATFORM)
    EEPROM.begin(512);
    Serial.begin(115200);
#elif defined(NRF51)
    // EEPROM.begin();
    Wire.setPins(DISPLAY_I2C_SDA_Pin, DISPLAY_I2C_SCL_Pin); // Have to change pin here since nrf51 dont have Wire.begin(SDA, SCL)
    Wire.begin();
    Wire.setClock(400000L);

    // force 12v power for now
    pinMode(4, OUTPUT);
    pinMode(7, OUTPUT);
    pinMode(6, OUTPUT);

    digitalWrite(4, LOW);
    digitalWrite(7, LOW);
    digitalWrite(6, HIGH);
#else
#error unsupported platform!
#endif

    // Init locale engine first, or gfx crashes
    lv_i18n_init(lv_i18n_language_pack);
    lv_i18n_set_locale(lv_i18n_language_pack[0]->locale_name);

    // TcMenu Initialize
    setupMenu();
    menuMgr.load(0xfade, storeNvsDefaults);

    // Reset language base on value loaded
    lv_i18n_set_locale(lv_i18n_language_pack[menuLanguage.getCurrentValue()]->locale_name);

    // Init Bluetooth
    setBluetoothOn(25);

    // Continue TcMenu Init
    installTheme();
    homePage();

    motorDirection = menuDirection.getBoolean();
    motorCurrent = menuCurrent.getCurrentValue();
    motorGear = menuGearTeeth.getCurrentValue();
    bpmTweak = menuBPMTweak.getLargeNumber()->getAsFloat();

    // Set serial pinout
#if defined(ESP_PLATFORM)
    DRIVER_SERIAL.begin(115200, SERIAL_8N1, MOTOR_SERIAL_RX_Pin, MOTOR_SERIAL_TX_Pin);
#elif defined(NRF51)
    DRIVER_SERIAL.setPins(MOTOR_SERIAL_RX_Pin, MOTOR_SERIAL_TX_Pin);
    DRIVER_SERIAL.begin(115200);
    vTaskDelay(100);
#else
#error unsupported platform!
#endif

    // Init TMC2209 driver
    powerSetup();
    driverSetup();
    setSpeed(0);
}

void loop()
{
    taskManager.runLoop();
    syncValuesFromBluetooth();
    checkPowerStatus();
}

// TcMenu 主题设置
static void installTheme()
{
#ifndef NRF51
    renderer.setTitleMode(BaseGraphicalRenderer::TITLE_FIRST_ROW);
    renderer.setUseSliderForAnalog(false);
    installMonoInverseTitleTheme(renderer, MenuFontDef(u8g2_wqy_14_project_orgel, 1), MenuFontDef(u8g2_wqy_14_project_orgel, 1), true);
    gfx.enableUTF8Print();    // 启用UTF-8以支持多语言
    gfx.setFontPosBaseline(); // 设置字体基线
#endif
}

// 向NVS中写入初始值
static void storeNvsDefaults()
{
#if defined(NRF51)
    EEPROM.format();
#endif

    menuMgr.save();
}

/*
    @brief Init power manager
*/
static void powerSetup()
{
    pm.begin();
    pm.acquireVoltage(menuVoltage.getCurrentValue());

    lastPowerStatus = false;
    menuPWRStatus.setCurrentValue(1);   // Set to "Error"
}

/*
    @brief Poll PG signal
*/
static void checkPowerStatus()
{
    uint8_t pg = pm.powerGood();
    if (lastPowerStatus != pg)
    {
        menuPWRStatus.setCurrentValue(pg + 1);
        lastPowerStatus = pg;
    }
}

/*
    @brief Init stepper driver
*/
static void driverSetup()
{
    pinMode(MOTOR_ENABLE_Pin, OUTPUT);    // 控制TMC2209使能引脚为输出模式
    digitalWrite(MOTOR_ENABLE_Pin, HIGH); // 将使能控制引脚设置为低电平从而让电机驱动板进入工作状态

    DRIVER_SERIAL.begin(115200); // 启动串口

    driver.begin();                       // 开始通讯
    driver.microsteps(DRIVER_MICROSTEPS); // 设置微步大小

    // 电流设置
    driver.rms_current(50); // 设置电流大小 (mA)

    digitalWrite(MOTOR_ENABLE_Pin, LOW); // 将使能控制引脚设置为低电平从而让电机驱动板进入工作状态
}

/*
    @brief Update motor operation params with UART
*/
static void updateMotorParams()
{
    if (playStatus)
    {
        // Set Motor Speed
        if (motorDirection)
        {
            driver.VACTUAL(playBPM * BPM_CALC_CONST / motorGear / 0.715 * bpmTweak);
        }
        else
        {
            driver.VACTUAL(-playBPM * BPM_CALC_CONST / motorGear / 0.715 * bpmTweak);
        }

        // Set Current
        driver.rms_current(motorCurrent); // 设置电流大小 (mA)
    }
    else
    {
        driver.VACTUAL(0);
        driver.rms_current(5);
    }
}

static void syncValuesFromBluetooth()
{
    if (ble_new_value_received)
    {
        menuBPM.setCurrentValue(ble_bpm_received);
        menuPlay.setBoolean(ble_play_status_received);
        ble_new_value_received = false;
    }
}

// 变更播放状态
void CALLBACK_FUNCTION switchPlayStatus(int id)
{
    if (menuPlay.getBoolean())
    {
        playStatus = true;
        updateMotorParams();
    }
    else
    {
        playStatus = false;
        updateMotorParams();
    }
}

// BPM改变回调
void CALLBACK_FUNCTION setSpeed(int id)
{
    playBPM = menuBPM.getCurrentValue();
    updateMotorParams();
}

// 设置电机运行方向
void CALLBACK_FUNCTION changeMotorDir(int id)
{
    motorDirection = !motorDirection;
    updateMotorParams();
}

// 返回首页
void CALLBACK_FUNCTION toHomePage(int id)
{
    menuMgr.save();

#if defined(ESP_PLATFORM)
    EEPROM.commit();
#endif
    renderer.takeOverDisplay();
}

// 设置齿轮齿数回调
void CALLBACK_FUNCTION setGearTeeth(int id)
{
    // TODO - your menu change code
    motorGear = menuGearTeeth.getCurrentValue();
    updateMotorParams();
}

// 电流数值改变回调函数
void CALLBACK_FUNCTION setCurrent(int id)
{
    motorCurrent = menuCurrent.getCurrentValue();
    updateMotorParams();
}

/*
    @brief  Callback function of menuLanguage
*/
void CALLBACK_FUNCTION setLanguage(int id)
{
    lv_i18n_set_locale(lv_i18n_language_pack[menuLanguage.getCurrentValue()]->locale_name);

    menuMgr.save();

#if defined(ESP_PLATFORM)
    EEPROM.commit();
#endif
    menuMgr.resetMenu(false);
}

/*
    @brief  Callback function of menuBluetooth
*/
void CALLBACK_FUNCTION setBluetoothOn(int id)
{
    if (menuBluetooth.getBoolean())
    {
        ble_on();
    }
    else
    {
        ble_off();
    }

    menuMgr.save();

#if defined(ESP_PLATFORM)
    EEPROM.commit();
#endif
}

/*
    @brief  Callback function of menuVoltage
*/
void CALLBACK_FUNCTION setPowerVoltage(int id)
{
    pm.acquireVoltage(menuVoltage.getCurrentValue());
#if defined(ESP_PLATFORM)
    EEPROM.commit();
#endif
}

void CALLBACK_FUNCTION setBpmTweak(int id)
{
    bpmTweak = menuBPMTweak.getLargeNumber()->getAsFloat();
#if defined(ESP_PLATFORM)
    EEPROM.commit();
#endif
}

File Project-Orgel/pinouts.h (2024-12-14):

#ifndef _PINOUTS_H_
#define _PINOUTS_H_

#if defined(ESP_PLATFORM)

#define MOTOR_ENABLE_Pin 33
#define MOTOR_SERIAL_RX_Pin 16
#define MOTOR_SERIAL_TX_Pin 17

#define DISPLAY_I2C_RST_Pin 255     // 255 == U8X8_PIN_NONE (keep default)
#define DISPLAY_I2C_SCL_Pin 255     // 255 == U8X8_PIN_NONE (keep default)
#define DISPLAY_I2C_SDA_Pin 255     // 255 == U8X8_PIN_NONE (keep default)

#define ENCODER_A_Pin 34
#define ENCODER_B_Pin 35
#define ENCODER_OK_Pin 32

#define CH224K_PG_Pin 255
#define CH224K_CFG1_Pin 255
#define CH224K_CFG2_Pin 255
#define CH224K_CFG3_Pin 255

#elif defined(NRF51)

#define MOTOR_ENABLE_Pin 16
#define MOTOR_SERIAL_RX_Pin 8
#define MOTOR_SERIAL_TX_Pin 9

#define DISPLAY_I2C_RST_Pin 255     // 255 == U8X8_PIN_NONE (keep default)
#define DISPLAY_I2C_SCL_Pin 24
#define DISPLAY_I2C_SDA_Pin 25

#define ENCODER_A_Pin 23
#define ENCODER_B_Pin 22
#define ENCODER_OK_Pin 21

#define CH224K_PG_Pin 5
#define CH224K_CFG1_Pin 4
#define CH224K_CFG2_Pin 7
#define CH224K_CFG3_Pin 6

#endif

#endif

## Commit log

2021-09-25 Code refactor. Now switch to tcMenu framework.
2021-09-29 Homepage is back. Hold the button to menu.
2022-01-23 Bugfix: current sensor code removed
    [Project-Orgel.ino]
2022-07-26 Bugfix: ENABLE_Pin 23 -> 33; Redundant code remove
    [Project-Orgel.ino]
2024-06-13 encoder input fix
2024-07-06 reduce ram usage & nrf51 nvs fix
    [Project-Orgel.ino]
2024-07-21 temporary force 12v power for nRF51
2024-07-27 readme update
    [BOM_Board1_Orgel nRF51_2024-07-24.xlsx, Support 1.STEP, Support 2.STEP]
2024-11-27 fixed ble on nRf51
    [Support 1.STEP]
2024-12-14 add "DRIVER_MICROSTEPS" marco
2024-12-14 Power manager for nRF51
